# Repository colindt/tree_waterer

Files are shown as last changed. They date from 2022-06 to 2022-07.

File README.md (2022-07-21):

# Tree Waterer

An Arduino-powered system for automatically watering a Christmas tree.

Sucessfully used by me to achieve fully-automatic zero-intervention watering over two Christmas seasons. Just set it up and let it do its thing.

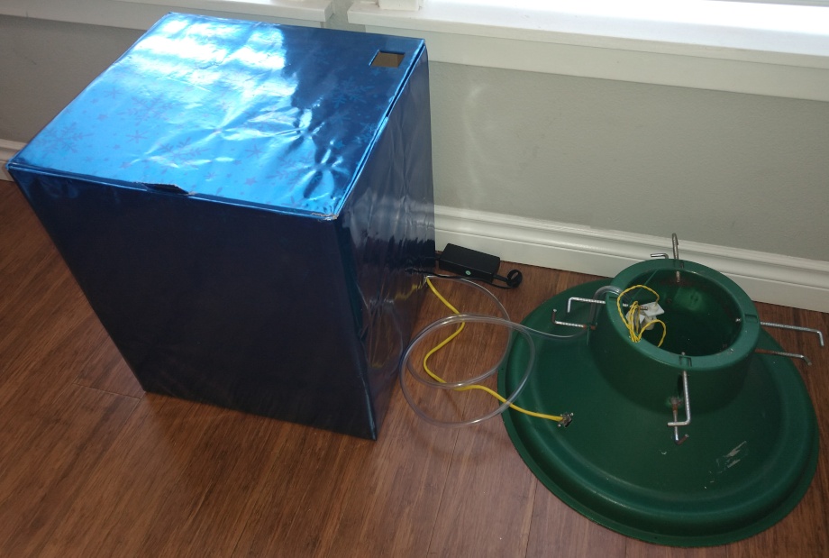
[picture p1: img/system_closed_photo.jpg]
system closed photo


[**More photos**](photos.md)

## How it Works

The watering device, consisting of a bucket of water and the main circuitry, sits next to the tree in a box disguised as a Christmas present. Water level sensors are mounted in the tree stand and connected to the Arduino over a Cat5 cable. When the sensors detect a low water level in the stand, the controller turns on a small water pump in the bucket to pump water into the stand through a length of plastic tubing. It then turns the pump off when the water level sensors again detect water.

There are four water sensors, and any one of them is enough to stop the pump, ensuring that a sensor failure is unlikely to overflow the stand and ruin the floor or surrounding gifts. Additionally, the sensors are "normally closed", meaning that accidentally unplugging them reads as "stand water full" to the controller, again ensuring that hardware failures don't ruin Christmas.

## The Waterer

Each of the four water level sensors in the stand has a corresponding green LED (LEDs 1-4) on the breadboard that shows its status ("on" for "water detected"). It's normal for some of these to never turn on if some of the sensors are mounted higher than the others. The orange LED5 turns on when the pump is running. LEDs 6-8 are used to indicate water level in the bucket, but they are unused in the current version.

The pump (shown below with a placeholder motor image) connects to the board through a spring terminal block. The block also has spots to plug in water level sensors to use in the bucket, but they are unused in this version.

The sensor board connects via an RJ45 jack.

### Breadboard view

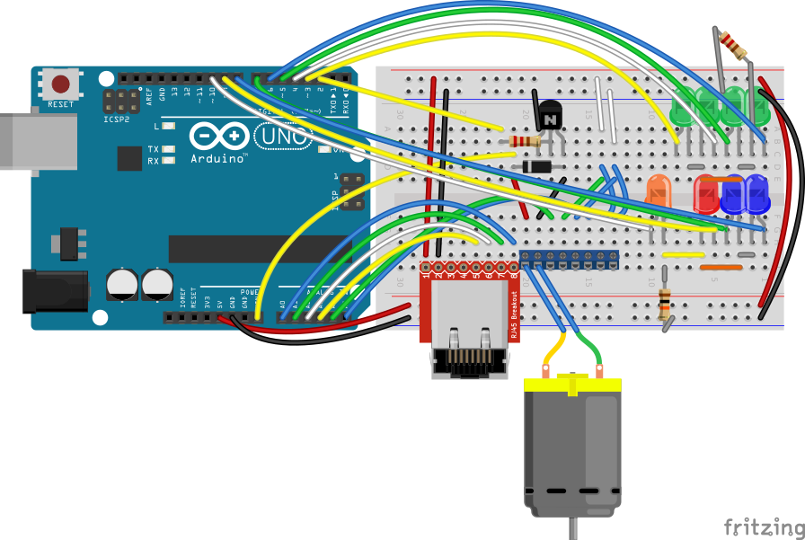
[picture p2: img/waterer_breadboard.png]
waterer breadboard view


### Schematic

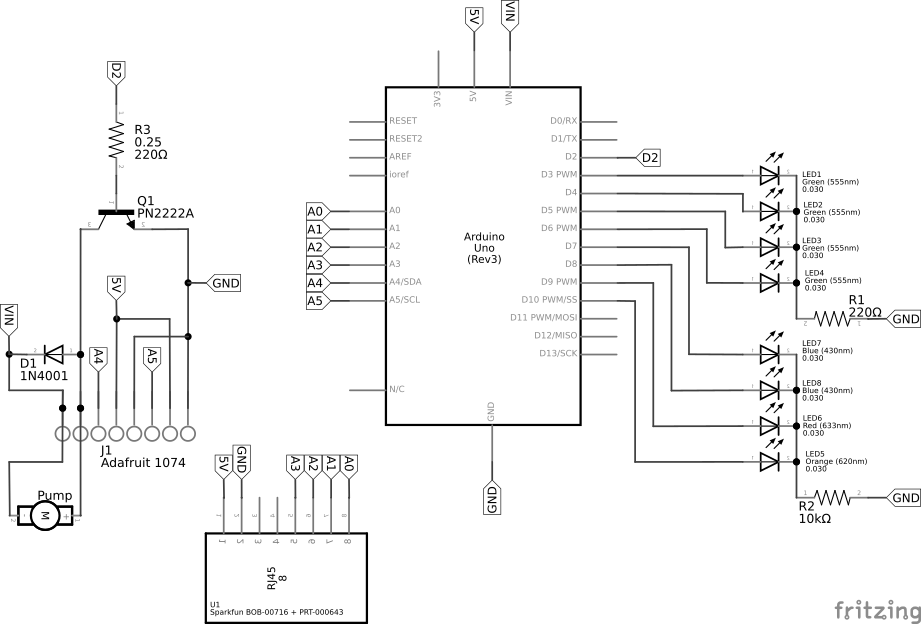
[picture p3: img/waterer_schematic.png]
waterer schematic


### Photo

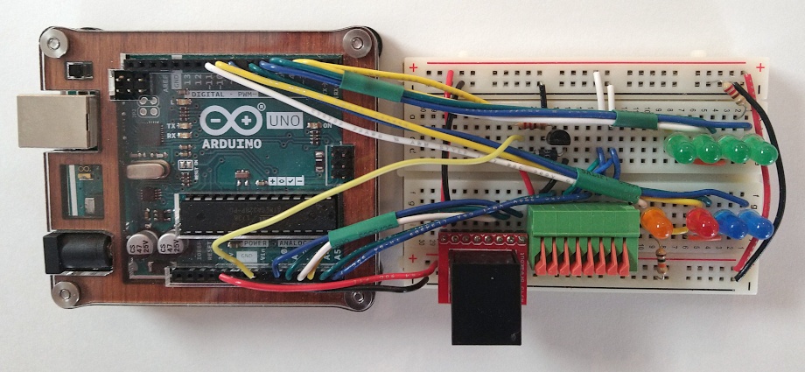
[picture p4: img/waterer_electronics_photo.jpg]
waterer electronics photo


## The Stand

The stand connects to the controller via an RJ45 jack mounted on the outside. On the underside of the stand is a breadboard that splits out the sensors. The sensors are shown as open pushbuttons in the image below. In reality, their switchs are normally closed, and open when water is detected.

The RJ45's pin 1 and the red wire on the left are unused in the current version.

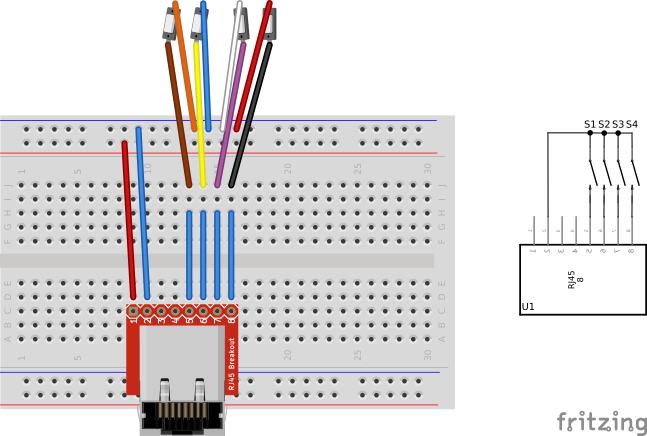
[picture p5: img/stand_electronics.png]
stand electronics


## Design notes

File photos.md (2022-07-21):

# Photo Gallery

## Closed view

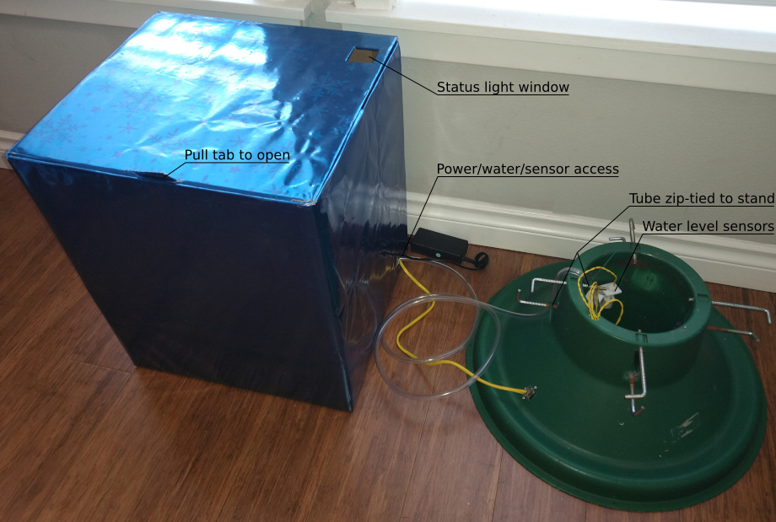
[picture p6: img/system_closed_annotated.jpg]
system closed photo annotated


The sensor cable and water tube can be hidden under a tree skirt in a real setup.

## Waterer

### Open view

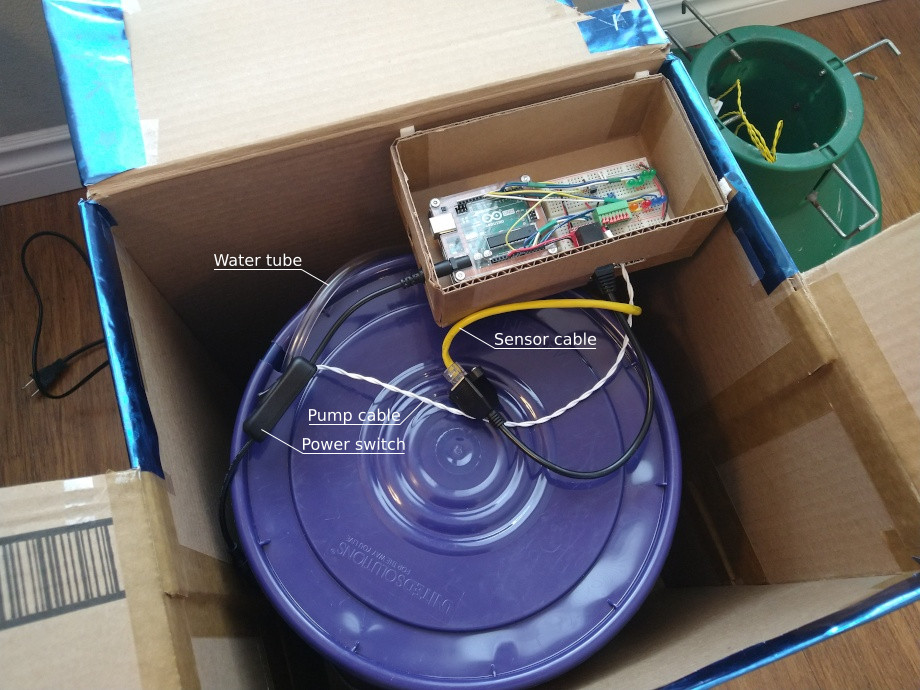
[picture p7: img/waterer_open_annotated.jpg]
waterer open photo annotated


A spare Cat5 panel mount/extender (shown here) is optional to make plugging and unplugging the sensor cable easier.

### Electronics

waterer electronics photo

### Bucket setup

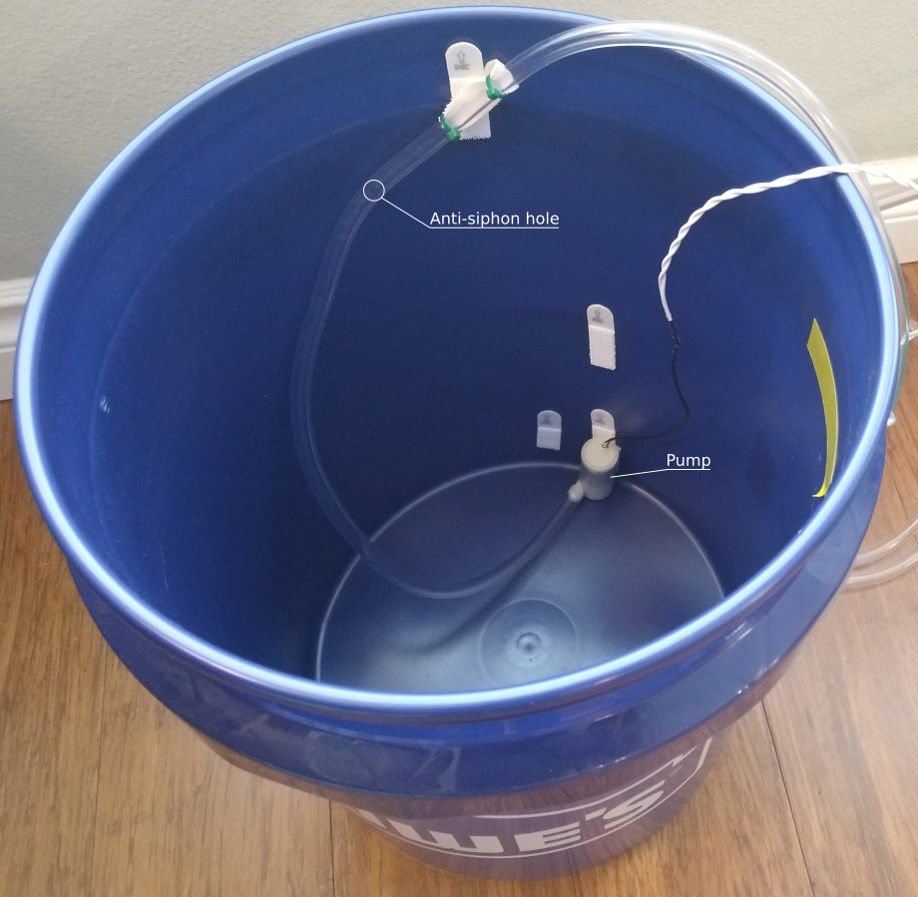
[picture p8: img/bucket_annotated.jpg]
bucket photo annotated


A small hole is drilled in the water tube inside the bucket but above the water line to prevent siphoning. When the pump is on, some water sprays out the hole. Make sure the lid is on tight and the spray is aimed away from the access hole so it all stays in the bucket.

## Stand

### Top view

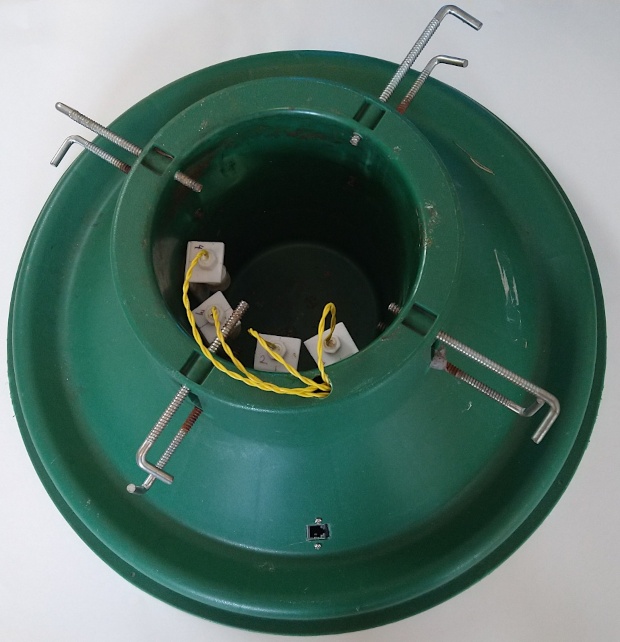
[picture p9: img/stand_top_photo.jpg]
stand top view photo


The tree supports on the side of the stand with the sensors are extended further to prevent the tree from hitting the sensors. The tree sits slightly off-center in the stand.

### Underside

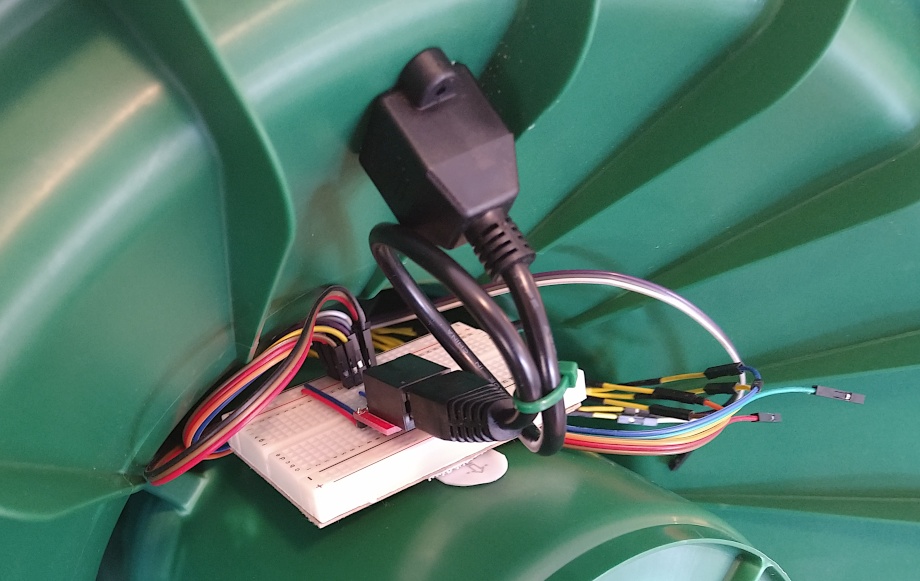
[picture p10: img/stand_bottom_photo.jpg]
stand bottom view photo


This could be done a lot cleaner. The extra wires are left over from a previous version that used a different type of sensor. The panel mount Cat5 extender allows plugging and unplugging the sensor cable even when the tree is in the stand.

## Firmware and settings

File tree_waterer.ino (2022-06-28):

const int TREE_N = 4;
const int PIN_TREE_SENSOR[] = {A0, A1, A2, A3}; //used as digital
const int PIN_TREE_LED[] = {3, 4, 5, 6};
int tree_sensor[4];

const int TANK_N = 2;
const int PIN_TANK_SENSOR[] = {A4, A5}; //used as digital
const int PIN_TANK_LED[] = {7, 8};
const int PIN_TANK_LED_EMPTY = 9;
int tank_sensor[2];

const int PIN_MOTOR = 2;
const int PIN_MOTOR_LED = 10;
bool motor_status = 0;


void setup() {
  for (int i = 0; i < TREE_N; i++) {
    pinMode(PIN_TREE_LED[i], OUTPUT);
    pinMode(PIN_TREE_SENSOR[i], INPUT_PULLUP);
  }

  for (int i = 0; i < TANK_N; i++) {
    pinMode(PIN_TANK_LED[i], OUTPUT);
    pinMode(PIN_TANK_SENSOR[i], INPUT_PULLUP);
  }
  pinMode(PIN_TANK_LED_EMPTY, OUTPUT);

  pinMode(PIN_MOTOR, OUTPUT);
  pinMode(PIN_MOTOR_LED, OUTPUT);

  Serial.begin(9600);
}


void loop() {
  tree_waterer();
}


void tree_waterer() {
  sensor_read_write();

  while (!any_tree_sensors_on()) {
    motor(1);
    sensor_read_write();
    delay(250);
  }
  motor(0);
  
  delay(250);
}


void sensor_read_write() {
  read_sensors();
  led_write();
  serial_write_sensors();
}


void read_sensors() {
  for (int i = 0; i < TREE_N; i++) {
    tree_sensor[i] = digitalRead(PIN_TREE_SENSOR[i]);
  }

  for (int i = 0; i < TANK_N; i++) {
    tank_sensor[i] = digitalRead(PIN_TANK_SENSOR[i]);
  }
}


void led_write() {
  for (int i = 0; i < TREE_N; i++) {
    digitalWrite(PIN_TREE_LED[i], tree_sensor[i]);
  }

  bool any_tank_sensors_on = false;
  for (int i = 0; i < TANK_N; i++) {
    if (tank_sensor[i]) {
      any_tank_sensors_on = true;
    }
    digitalWrite(PIN_TANK_LED[i], tank_sensor[i]);
  }

  digitalWrite(PIN_TANK_LED_EMPTY, !any_tank_sensors_on);
}


void serial_write_sensors() {
  String sep = F(", ");
  
  Serial.print(F("tree: "));
  for (int i = 0; i < TREE_N; i++) {
    Serial.print(tree_sensor[i]);
    Serial.print(sep);
  }

  Serial.print(F("| tank: "));
  for (int i = 0; i < TANK_N; i++) {
    Serial.print(tank_sensor[i]);
    Serial.print(sep);
  }

  Serial.print(F("| motor: "));
  Serial.print(motor_status);
  
  Serial.println();
}


bool any_tree_sensors_on() {
  bool result = false;
  for (int i = 0; i < TREE_N; i++) {
    if (tree_sensor[i]) {
      result = true;
      break;
    }
  }
  return result;
}


void motor(bool status_) {
  motor_status = status_;
  digitalWrite(PIN_MOTOR,     status_);
  digitalWrite(PIN_MOTOR_LED, status_);
}


void led_test() {
  for (int i = 0; i < TREE_N; i++) {
    blink_led(PIN_TREE_LED[i]);
  }

  blink_led(PIN_TANK_LED_EMPTY);
  
  for (int i = 0; i < TANK_N; i++) {
    blink_led(PIN_TANK_LED[i]);
  }
  
  blink_led(PIN_MOTOR_LED);
}


void blink_led(int pin) {
  digitalWrite(pin, HIGH);
  delay(500);
  digitalWrite(pin, LOW);
}


void motor_test() {
  motor(1);
  delay(2000);
  motor(0);
  delay(2000);
}

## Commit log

2022-06-28 using a different type of sensor now
2022-07-21 non-placeholder rj45 part
    [tree_stand.fzz, tree_waterer.fzz]
